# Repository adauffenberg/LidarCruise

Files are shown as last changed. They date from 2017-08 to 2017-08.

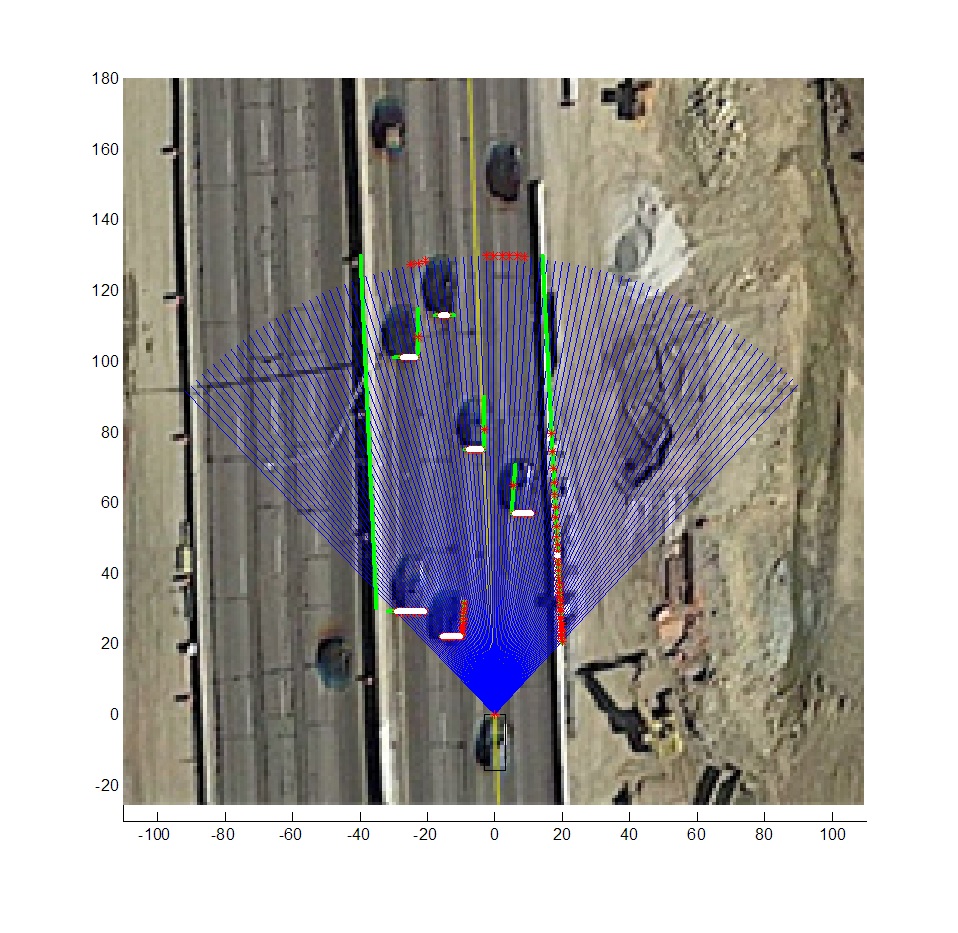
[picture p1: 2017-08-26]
Matlab/test3.jpg

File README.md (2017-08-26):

# LidarCruise

Lidar Cruise is a level 1 autonomous active cruise control system for my 2005 Mazda6. By interfacing with my steering wheel cruise control buttons and a Lidar unit, the distance to the object ahead can be varied.

Pleae read this projects website first for a overview of the system. This will aid in understanding of the files here.

Included in this Repo:

## 2 Matlab files and jpg image: 
These were used during conceptualization of the project. Although not used on the final hardware for various reasons, they provided valuable knowledge at the start. Scene_creation.m builds a environment based off my manual graphing of green lines on satellite image. Basically creates a 2d model for the next matlab file to interact with. ACC_code_tests.m runs a "virtual lidar" by firing blue beams, collisions are red points. Objects from scene_creation.m are identified based on size, angle, and position of the red points and are marked in white. This code is very matrix heavy, probably too much to run on an Arduino. Hence, a much simplified code is run on final arduino hardware.

## 4 Arduino Ino files:
These run on the 4 arduinos that make up Lidar Cruise

LidarACC:

Central brain. Gathers Lidar data and data from other arduinos. Also called Arduino 3

VSS_ACC: 

Reads VSS wire, passes vehicle speed to central brain upon request, also called Arduino 2

MirrorACC:

Controls motor that Lidar is mounted on, as well as reading photogates. Sends trigger to central brain when photogate is triggered from motor rotation, starting main loop in central brain. Essentially a clock for the entire system. Also called Arduino 1.

ControlACC:

Reads from steering wheel buttons and central brain, decides what relay/resistor to switch. This controls the car cruise control module set speed. Based on my SteeringWheelControl repo code. Also called Arduino 4.

## 1 Fritzing file: 
This file allowed planning of wiring for Lidar Cruise

## 1 Blender file: 
This object was 3D printed, allowing waterproof connection of the Lidar tube and flat window. Needed since the Lidar was not looking through a curved window directly attached to the tube. 

##

Please note: This code is provided for informational use only. Don't do anything stupid with it that may harm anyone or anything. Remember, a level 1 autonomous system requires driver interaction at all times, who is ultimately responsible for the vehicle.

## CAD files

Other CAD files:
front3.blend

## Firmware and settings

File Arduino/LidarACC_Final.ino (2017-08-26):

#include <LIDARLite.h>
#include <Wire.h>
#include <SoftwareSerial.h>
SoftwareSerial mySerial(69,3); // RX, TX
#include <VirtualWire.h>

// Create a new LIDARLite instance
LIDARLite myLidarLite;

//IMU initialization
const int MPU_addr=0x68;  // I2C address of the MPU-6050
int16_t AcX,AcY,AcZ,Tmp,GyX,GyY,GyZ;


int distances[120];
int times[120];
int i=0;
int start=0;
int finish=0;
int xlist[120];
int ylist[120];
int positiontrigger=0;
int cruisestate=0;
int loopmax=0;
int objectdis=6000;
int prevobjectdis=0;
int objectwidth=0;
int counter=0;
int reaction=0;
int deltav=0;
byte velocity=0;
byte set=0;
int skip=0;
int bluetoothsend=0;
int incomingByte=0;
int motorcommand=0;
int speedloop=0;
int loopcounter=0;
int ftobjectdis = 0;
int controlincoming=0;

void setup() {
  
  Serial.begin(115200);
  Serial1.begin(19200);
  Serial2.begin(9600);
  Serial3.begin(9600);
  mySerial.begin(9600);
  
  set=0;
  
  
 
  //IMU config
  Wire.begin();
  Wire.beginTransmission(MPU_addr);
  Wire.write(0x6B);  // PWR_MGMT_1 register
  Wire.write(0);     // set to zero (wakes up the MPU-6050)
  Wire.endTransmission(true);
  
  
  myLidarLite.begin(0,true);
  myLidarLite.configure(0);
  
}


void loop()
{ 
  //Read photodiode gate level
  if (mySerial.available()) {
    incomingByte = mySerial.read();
    //Serial.print(incomingByte); 
  
   
   //Only start reading process when triggered by serial command of 2 from mirror arduino(read as 50)
  if (incomingByte==50){
     
  
   
    
    /////////////////////////////////////////////LIDAR///////////////////
    
    
    //Adjust this delay until mirror lines up with opening
    //delay(220); //0
    
    start=millis();
    
   
  for(int i = 0; i < 120; i++){
    distances[i]=myLidarLite.distance(false); 
    
    //get time to from start of loop to current measurement
    finish=millis();  
    times[i]=finish-start;
    //when beyond 60 degrees (332 ms) stop gathering lidar points
    if (times[i]>332){
      loopmax=i;
      break;
     
    }
    else{
      loopmax=119;
    }
  }
  
  
  //convert to x,y
    for (i=0;i<loopmax;i++){
      
    if (distances[i]>120){
    xlist[i]=-distances[i]*cos(PI/180*(115-((times[i]-40)*0.18))); //0.18
    ylist[i]=distances[i]*sin(PI/180*(115-((times[i]-40)*0.18)));
    }
    else
    {
      xlist[i]=0;
      ylist[i]=0;
    }
    /*
    Serial.print(xlist[i]);
    Serial.print("\t");
    Serial.print(ylist[i]);
    Serial.println("\t");
    */
    } 
   
    
    //Run once with bias correction, this will be immediately overwritten in the next for loop
    distances[0]=myLidarLite.distance();
    
   
 /////////////////////////////////////////////VSS///////////////////


 Serial1.print(0);
 
   if (Serial1.available()) {
    delay(50);
    velocity = Serial1.read();
   }
   if (set==0){
     set=velocity;
         
   }
  
 
delay(10);

 
 /////////////////////////////////////////////IMU///////////////////
  
  

 Wire.beginTransmission(MPU_addr);
  Wire.write(0x3B);  // starting with register 0x3B (ACCEL_XOUT_H)
  Wire.endTransmission(false);
  Wire.requestFrom(MPU_addr,14,true);  // request a total of 14 registers
  AcX=Wire.read()<<8|Wire.read();  // 0x3B (ACCEL_XOUT_H) & 0x3C (ACCEL_XOUT_L)    
  AcY=Wire.read()<<8|Wire.read();  // 0x3D (ACCEL_YOUT_H) & 0x3E (ACCEL_YOUT_L)
  AcZ=Wire.read()<<8|Wire.read();  // 0x3F (ACCEL_ZOUT_H) & 0x40 (ACCEL_ZOUT_L)
  Tmp=Wire.read()<<8|Wire.read();  // 0x41 (TEMP_OUT_H) & 0x42 (TEMP_OUT_L)
  GyX=Wire.read()<<8|Wire.read();  // 0x43 (GYRO_XOUT_H) & 0x44 (GYRO_XOUT_L)
  GyY=Wire.read()<<8|Wire.read();  // 0x45 (GYRO_YOUT_H) & 0x46 (GYRO_YOUT_L)
  GyZ=Wire.read()<<8|Wire.read();  // 0x47 (GYRO_ZOUT_H) & 0x48 (GYRO_ZOUT_L)
  //Serial.print("AcX = "); Serial.print(AcX);
  //Serial.print(" | AcY = "); Serial.print(AcY);
  //Serial.print(" | AcZ = "); Serial.print(AcZ);
  //Serial.print(" | Tmp = "); Serial.print(((Tmp/340.00+36.53)*(9/5))+32);  //equation for temperature in degrees C from datasheet
  //Serial.print(" | GyX = "); Serial.print(GyX);
  //Serial.print(" | GyY = "); Serial.print(GyY);
  //Serial.print(" | GyZ = "); Serial.println(GyZ);
  
 
 //IMU Correction of LIDAR 
 //Zero rate value too high, keep for temp reading for debug, IMU correction of lidar around turn not possible
 
 /////////////////////////////////////////////DECISION/SENDING///////////////////
 
 /*
  1 - short press coast
  2 - short press accel
  3 - long press coast
  4 - long press accel
  */
 
  
 prevobjectdis=objectdis;
 objectdis=6000;
 
 objectwidth=0;
 counter=0;
 
 skip=0;
 
  for (i=0;i<(loopmax-1);i++){
    //Find width of object (defn: <3ft (90cm) distance difference between points), if greater than 300cm (10ft) and with 20ft on either side of front, don't react, probably road sloping up into sensor
    if (((ylist[i+1]-ylist[i])<90) && (xlist[i+1]<600) && (xlist[i+1]>-600)) {
      counter=counter+1;
    }
    else {
      if (counter>2) {
        objectwidth=xlist[i]-xlist[i-counter];
        if (objectwidth>300) {
          skip=1;
        }
        counter=0;
      }
      else {
        counter=0;  
      }  
    }
    
    
    //Check each point to see if it is within 152 cm (5ft) of either side of center and less than the previous closest distance
    if ((xlist[i]<152) && (xlist[i]>-152) && (ylist[i]<objectdis) && (ylist[i]>0)) {
      objectdis=ylist[i];
    }
  }
  
  //Serial2.print(" Distance ");
  //Serial2.print(objectdis);
  //Serial2.print(" ");
  
  
  cruisestate=analogRead(A0);
  
  
  deltav=(prevobjectdis-objectdis)*1.5;
  
  //If cruise is not on, do not react
  if (cruisestate>575) {
    reaction=6;
    bluetoothsend=1;
  }
  //If object was determined above to be too wide, don't react
  else if (skip==1) {
    reaction=0;
    skip=0;
    bluetoothsend=2;
  }
  //If deltav > 178 cm/s (4mph), long press coast
  else if (deltav>178) {
    reaction=3;
    bluetoothsend=3;
  }
  //If speed no signal, don't react, (kinda outdated, meant for no GPS, should never enter)
  else if (velocity<0) {
    reaction=0;
    bluetoothsend=13;
  }
  //If velocity is over set speed, short press coast
  else if (velocity>(set+2)) {
    reaction=1;
    bluetoothsend=4;
  }
  //If deltav < 134 cm/s (-3mph) and velocity below 3mph below set, long press accel
  else if ((deltav<-134) && (velocity<(set-3))) {
    reaction=4;
    bluetoothsend=5;  
  }
  //If deltav < 134 cm/s (-3mph) and velocity above 3mph below set, short press accel
  else if ((deltav<-134) && (velocity>=(set-3)) && (velocity<set)) {
    reaction=2;
    bluetoothsend=6;
  }
  else {
    //If distance less than 70ft, long press coast
    if (objectdis<2100) {
      reaction=3;
      bluetoothsend=7;
    }
    //If distance greater than 130 ft and velocity below 3mph below set, long press accel if previous was short press accel, if not short press
    else if ((objectdis>4000) && (velocity<(set-3))) {
      if (reaction==2 || reaction==4){
        reaction=4;
      }
      else {
        reaction=2;
      }
      bluetoothsend=8;
    }
    //If distance greater than 130 ft and velocity above 3mph below set, short press accel
    else if ((objectdis>4000) && (velocity>=(set-3)) && (velocity<set)) {
      reaction=2;
      bluetoothsend=9;
    }
    //If distance greater than 110 ft and deltav less than 0 and previous press was not short press accel, short press accel
    else if ((objectdis>3300) && (deltav<0) && (reaction!=2)) {
      reaction=2;
      bluetoothsend=10;
    }
    //If distance less than 100 ft and deltav greater than 0, short press coast 
    else if ((objectdis<3000) && (deltav>0)) {
      reaction=1;
      bluetoothsend=11;
    }
    //If none of the above, do nothing
    else {
      reaction=0;
      bluetoothsend=12;
    }
  }
      
 //if prev distance =6000 (not in range) change long press coast into short press
 if (prevobjectdis==6000 && reaction==3) {
   reaction=1;
 }
  
 // send reaction to control arduino 
 
 if (reaction<6) {  
 Serial3.print(reaction);
 }
 
 //read from control arduino if available and increase or decrease set speed
 if (Serial3.available()) {
   controlincoming = Serial3.read();
    if (controlincoming == 48) {
      set = set+1;
    }
    else if(controlincoming == 49) {
      set = set -1;
      if (set<0){
        set=0;
      }
    }
    
 }
 
     
 /////////////////////////////////////////////BLUETOOTH///////////////////
  
  Serial2.print("#");
  
  if (set<10){
    Serial2.print("00");
  }
  else {
    Serial2.print(set);
  }
  
  if (velocity<10){
    Serial2.print("00");
  }
  else {
    Serial2.print(velocity);
  }
  
  Serial2.print(reaction);
  
  ftobjectdis=objectdis/30.48;
  Serial2.print(ftobjectdis);
  
  Serial2.print("~");
  
  //Original bluetooth debug code
 /* 
 
 //Serial2.println("test"); 
 if (bluetoothsend==1) {
   Serial2.println("Cruise Off");
 }
 else if (bluetoothsend==2) {
   Serial2.println("Hill: No reaction");
 }
 else if (bluetoothsend==3) {
   Serial2.println("Closing speed >6mph, long press coast");
 }
 else if (bluetoothsend==13) {
   Serial2.println("No GPS");
 }
 else if (bluetoothsend==4) {
   Serial2.println("Greater than set speed, short press coast");
 }
 else if (bluetoothsend==5) {
   Serial2.println("Leaving speed >6mph, >3mph below set, long press accel");
 }
 else if (bluetoothsend==6) {
   Serial2.println("Leaving speed >6mph, <3mph below set, short press accel");
 }
 else if (bluetoothsend==7) {
   Serial2.println("Closer than 40ft, long press coast");
 }
 else if (bluetoothsend==8) {
   Serial2.println("Greater than 130ft, >3mph below set, long press accel");
 }
 else if (bluetoothsend==9) {
   Serial2.println("Greater than 130ft, <3mph below set, short press accel");
 }
 else if (bluetoothsend==10) {
   Serial2.println("Greater than 110ft, deltav<0, short press accel");
 }
 else if (bluetoothsend==11) {
   Serial2.println("Less than 80ft, deltav>0, short press coast");
 }
 else if (bluetoothsend==12) {
   Serial2.println("Else: Do nothing");
 }
 */
 
 //Check and see how long each loop takes
 //Serial.print(millis());
  //  Serial.println(" ");
    
 }////END OF POSITION TRIGGERED LOOP
 }////END OF  SERIAL READ TRIGGERED LOOP
 
 //When in motor fault mode, wait for bluetooth commands to manually rotate motor
 if (incomingByte<50) {
   //Serial.println(incomingByte);
   if (incomingByte==48) {
     Serial2.println("Motor error: Cannot find start position");
   }
   else if (incomingByte==49) {
     Serial2.println("Motor error: Out of range");
   }
   //Look for bluetooth command. If 0 (48) is read, send 0 to mirror arduino to turn left, if 1 (49) is read, send 1 to mirror arduino to turn right
   if (Serial2.available()) {
    motorcommand = Serial2.read();
    if (motorcommand==48) {
      mySerial.print(0);
    }
    else if (motorcommand==49) {
      mySerial.print(1);
    }
   }
 } 
 
 
  
 }
  

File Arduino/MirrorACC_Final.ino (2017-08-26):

#include <Stepper.h>
#include <SoftwareSerial.h>

const int stepsPerRevolution = 200;  

// initialize the stepper library on pins 3 through 6:
Stepper myStepper(stepsPerRevolution, 3, 4, 5, 6);
int positionmain=0;
int positionerror=0;
int counter=0;
int incomingByte=0;

SoftwareSerial mySerial(9, 10); // RX, TX

void setup() {
  
 
// set the speed at 60 rpm:
  mySerial.begin(9600);
  Serial.begin(9600);
  myStepper.setSpeed(30);
  positionmain=analogRead(A3);
  positionerror=analogRead(A4);

  //Rotate right to left until position sensor is triggered or more than 35 steps, (initialize start position)
    while(positionmain>10 && counter<36 && positionerror>10) {
      myStepper.step(-1);
      positionmain=analogRead(A3);
      positionerror=analogRead(A4);
      //Serial.println(positionmain);
      //Serial.println(positionerror);
      //Serial.println(counter);
      counter=counter+1;
      }
     //if start position not found, write 0 to serial for "cannot find start error" and wait for command from serial to manually move left or right
     if (counter>35) {
       Serial.println("initialize start error");
       mySerial.print(0);
       while (counter>35) {
         incomingByte=0;
         if (mySerial.available()) {
           incomingByte = mySerial.read();
         }
         //If 0 is sent, move left 18 degrees
         if (incomingByte==48) {
           myStepper.step(-10);
         }
         //If 1 is sent, move right
         else if (incomingByte==49) {
           myStepper.step(10);
         }
       }
     }
   
     //if error position gate (180 degrees around) is triggered, write 1 to serial for "out of range error" and wait for command from serial to manually move left or right
     else if (positionerror<11) {
       Serial.println("initialize out of range error");
       mySerial.print(1);
       while (positionerror<11) {
         incomingByte=0;
         if (mySerial.available()) {
           incomingByte = mySerial.read();
         }
         //If 0 is sent, move left
         if (incomingByte==48) {
           myStepper.step(-10);
         }
         //If 1 is sent, move right
         else if (incomingByte==49) {
           myStepper.step(10);
         }
       }
     }
     
     counter=1;
     delay(200);
}


void loop() {
  // step 60 degrees right:
  myStepper.step(33);
  //if never entered loop to step left (counter=0), through error wait for manual movement
  if (counter==0) {
    Serial.println("no steps to the left error");
       mySerial.print(0);
       while (counter==0) {
         incomingByte=0;
         if (mySerial.available()) {
           incomingByte = mySerial.read();
         }
         //If 0 is sent, move left 18 degrees
         if (incomingByte==48) {
           myStepper.step(-10);
         }
         //If 1 is sent, move right
         else if (incomingByte==49) {
           myStepper.step(10);
         }
       }
     }
   counter=0;
  // step left until 
  positionmain=analogRead(A3);
  positionerror=analogRead(A4);
  //Serial.println(positionmain);
  //Serial.println(counter);
  //Serial.println(positionerror);
 while (positionmain>10 && counter<20 && positionerror>10) {
    myStepper.step(-2);
      positionmain=analogRead(A3);
      positionerror=analogRead(A4);
      //Serial.println(positionmain);
      //Serial.println(positionerror);
      //Serial.println(" ");
      counter=counter+1;
  }
  //if start position not found, write 0 to serial for "error" and wait for command from serial to manually move left or right  
    if (counter>19) {
      Serial.println("start error");
       mySerial.print(0);
       while (counter>19) {
         incomingByte=0;
         if (mySerial.available()) {
           incomingByte = mySerial.read();
         }
         //If 0 is sent, move left 18 degrees
         if (incomingByte==48) {
           myStepper.step(-10);
         }
         //If 1 is sent, move right
         else if (incomingByte==49) {
           myStepper.step(10);
         }
       }
     }
    //if error position gate (180 degrees around) is triggered, write 1 to serial for "error" and wait for command from serial to manually move left or right 
    else if (positionerror<11) {
     Serial.println("out of range error"); 
     mySerial.print(1);
     while (positionerror<11) {
         incomingByte=0;
         if (mySerial.available()) {
           incomingByte = mySerial.read();
         }
         //If 0 is sent, move left
         if (incomingByte==48) {
           myStepper.step(-10);
         }
         //If 1 is sent, move right
         else if (incomingByte==49) {
           myStepper.step(10);
         }
     }
   }
   
   //If not two above error must have exited while loop due to position main trigger, send command to lidar arduino
   else if (positionmain<11) {
     mySerial.print(2);
     //Serial.println("sent");
  
}
   
}
  
  

  
